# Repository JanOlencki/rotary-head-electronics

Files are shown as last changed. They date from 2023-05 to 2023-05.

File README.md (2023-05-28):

# PCB for the Rotary Head Controller
This repository is a part of a larger project. The description of it can be found in the [rotary-head-software](https://github.com/JanOlencki/rotary-head-software) repository.

## Features
* Comunication via RS-485 standard (terminating resistor included)
* STM8 microcontroller (SWIM programming interface exposed on pin header)
* One connector (RJ-45) for both communication and power supply
* Stepper motor control using the *Allegro A5977* driver
* Adjustment of the stepper motor current
* Electrostatic discharge protection
* Over-current protection (using a resettable fuse)
* Step down voltage conversion for a digital part (EMI filter included)

## Manufacturing and Assembly 
The PCB is designed to be manufactured on a double-sided FR4 laminate (1.5mm thick) with 35&mu;m thick copper. It's recommended to solder all parts by hand.

## Repository contents
* Schematic
* Board GERBER and Drill files
* Bill of Materials

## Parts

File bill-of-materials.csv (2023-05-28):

Designators | Description | Value | Quantity
C1, C6, C7, C8, C9, C13, C15 | 220nF, 16V, 0805 | 220nF | 7
C2, C3, C4 | Panasonic, EEEFK1E220R, 22μF, 25V | 22μF/25V | 3
C5 | 470pF, 16V, 0805 | 220pF | 1
C10, C11 | Panasonic, EEEFPE561UAP, 560μF, 25V | 560μF/25V | 2
C12, C16 | 680pF, 16V, 0805 | 680pF | 2
C14, C17, C19 | 100nF, 16V, 0805 | 100nF | 3
C18 | 1μF, 16V, 0805 | 1μF | 1
F1 | ECE, SL150-33, 1.5A, 33V | 1.5A | 1
J1 | Connfly, DS1021-1X2SF162-B, 1x2 pin header, 2.54mm raster |  | 1
L1 | Viking, NL12KTC120, 12μH, 500mA, 600mΩ, 1812 | 12μH/500mA | 1
R1 | 100Ω, 250mW, 1206 | 100Ω | 1
R2 | 0Ω, 125mW, 0805 | Placeholder, not soldered | 1
R3 | 36kΩ, 125mW, 0805 | 36kΩ | 1
R4 | SR Passives, T67W-20K, 20kΩ, 250mW, linear | 20kΩ | 1
R5 | 56kΩ, 125mW, 0805 | 10kΩ | 1
R6, R9, R10 | 56kΩ, 125mW, 0805 | 56kΩ | 3
R11 | 82Ω, 125mW, 0805 | 82Ω | 1
R7, R8 | 220mΩ, 1%, 250mW, 1206 | 220mΩ/1% | 2
S1 | C&K, KMR241G, Microswitch, SPST-NO |  | 1
U1 | STMicroelectronics, ST3485EBDR, 15 kV ESD protection, 3.3V, RS-485, 12 Mbps, SO8 | ST3485EBDR | 1
U2 | STMicroelectronics, STM8L101K3T6, ARM-based 8-bit MCU, 8 kB Flash, 1.5 kB Internal RAM, 32-pin LQFP | STM8L101K3T6 | 1
U3 | Allegro Microsystems, A5977, Stepper motor driver, 28-pin TSSOP | A5977 | 1
U4 | Aimtec, AMSRL-783.3JZ, DC-to-DC converter, 3.3V, 500mA | AMSRL-783.3JZ | 1
X1 | Attend, 210A-11C0A-R, RJ45 jack shielded |  | 1
X2, X3 | Hirose, DF3-4P-2DSA, 4-pin connector, 2mm raster |  | 2

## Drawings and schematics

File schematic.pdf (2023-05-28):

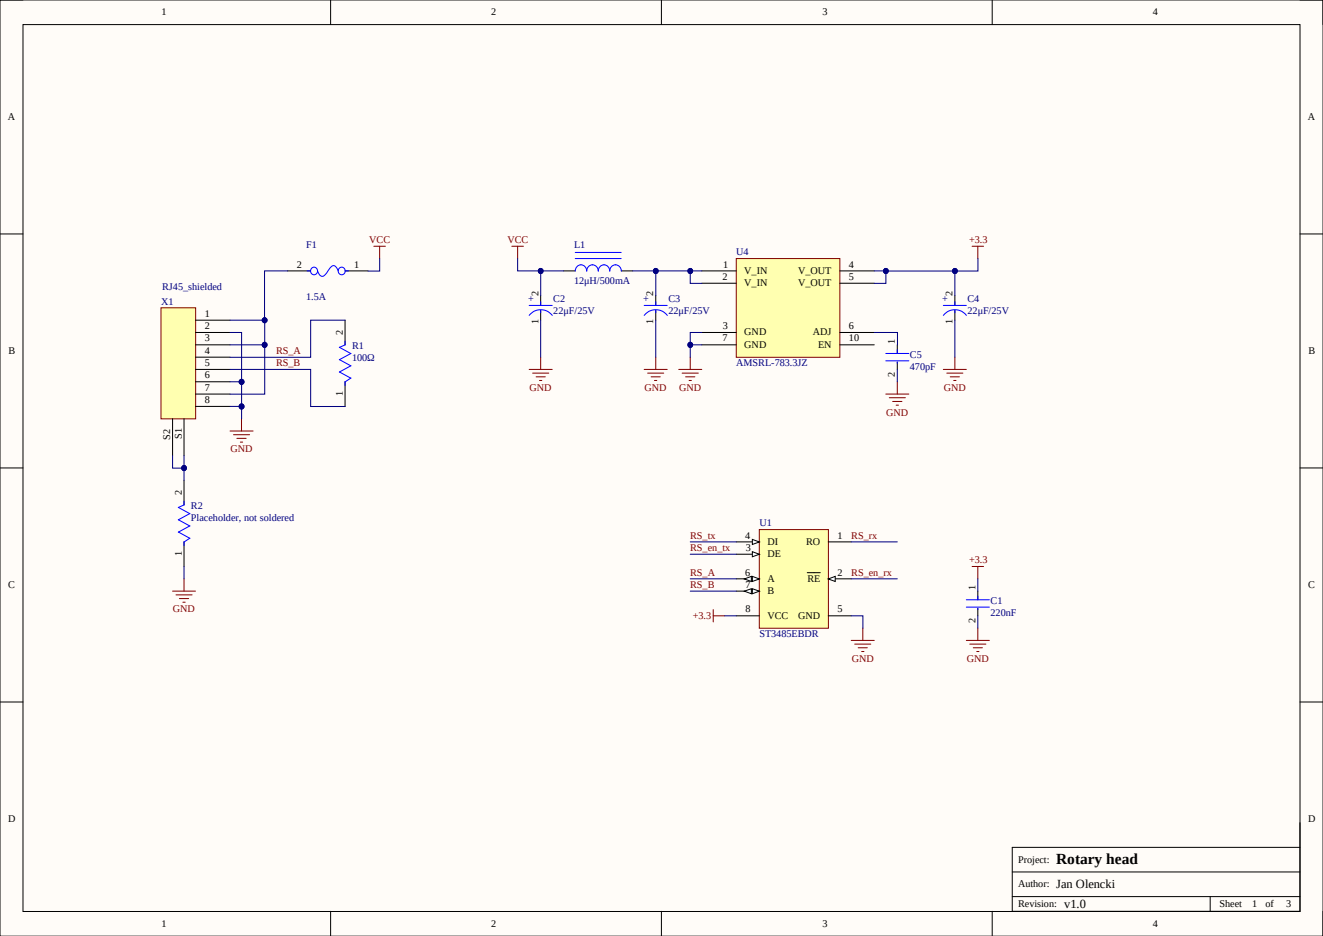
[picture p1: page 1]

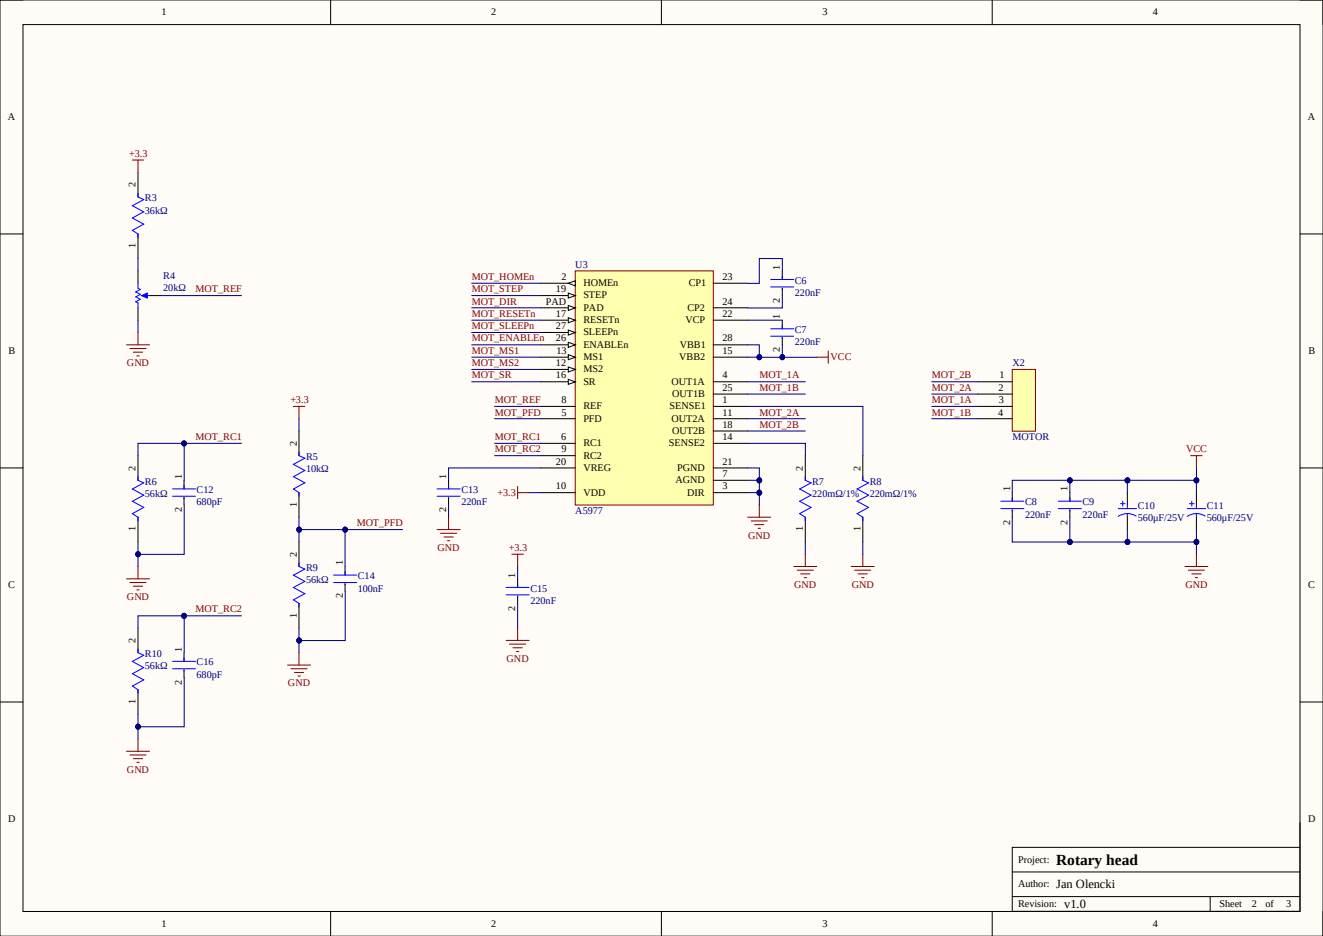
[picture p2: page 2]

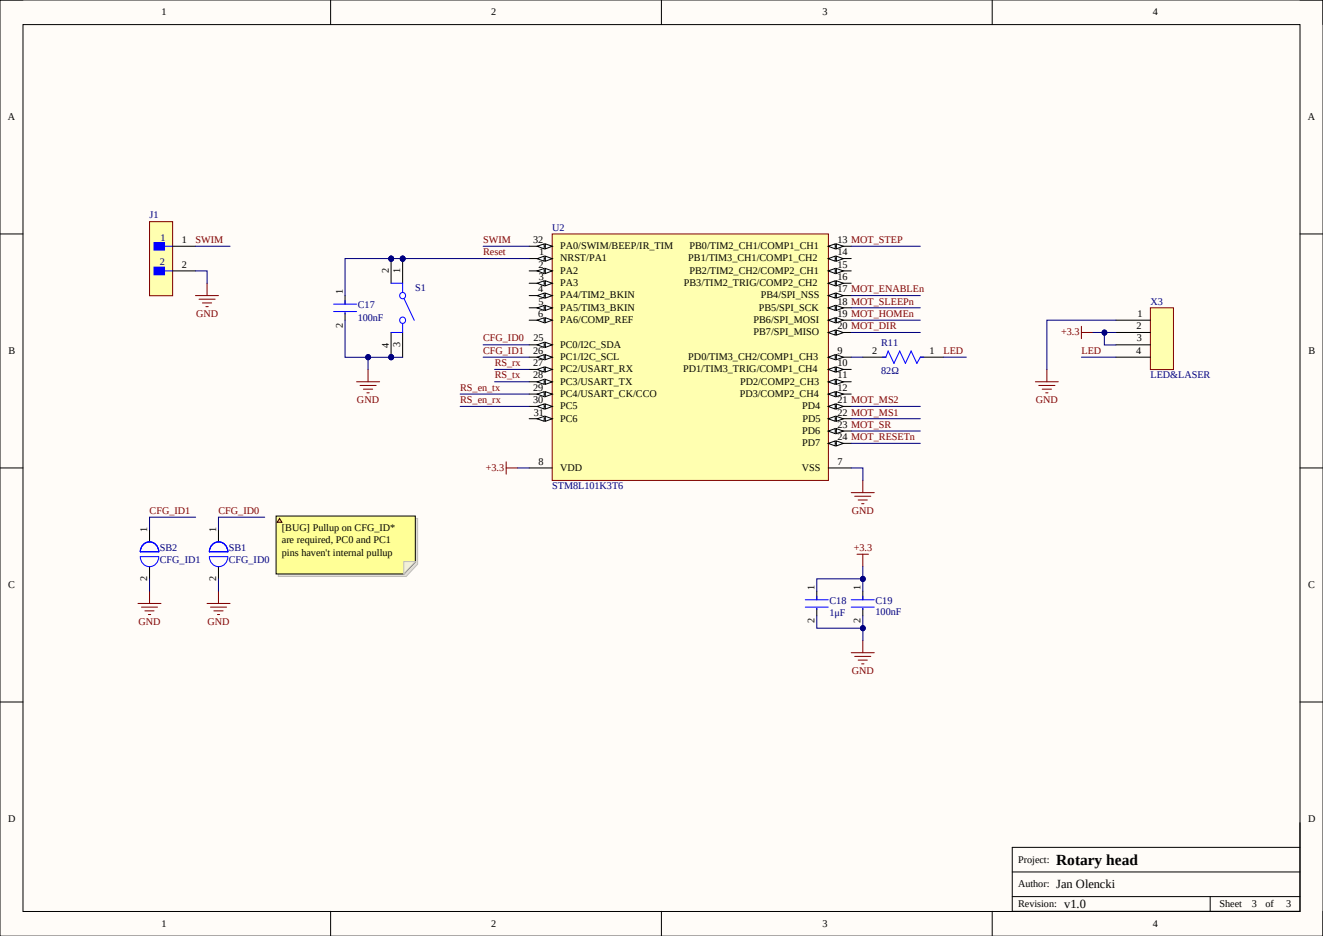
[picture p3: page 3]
PA0/SWIM/BEEP/IR_TIM 32 NRST/PA1 1 PA2 2 PA3 3 PA4/TIM2_BKIN 4 PA5/TIM3_BKIN 5 PA6/COMP_REF 6; PB0/TIM2_CH1/COMP1_CH1; PB1/TIM3_CH1/COMP1_CH2; PB2/TIM2_CH2/COMP2_CH1; PB3/TIM2_TRIG/COMP2_CH2; PB4/SPI_NSS; PB5/SPI_SCK; PB6/SPI_MOSI; PB7/SPI_MISO; PC0/I2C_SDA 25 PC1/I2C_SCL 26 PC2/USART_RX 27 PC3/USART_TX 28 PC4/USART_CK/CCO 29 PC5 30 PC6 31; PD0/TIM3_CH2/COMP1_CH3; PD1/TIM3_TRIG/COMP1_CH4; PD2/COMP2_CH3; PD3/COMP2_CH4; VDD 8; VSS; STM8L101K3T6; GND; LED&LASER; LED; SWIM; MOT_HOMEn; MOT_STEP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

[BUG] Pullup on CFG_ID*
are required, PC0 and PC1
pins haven't internal pullup
